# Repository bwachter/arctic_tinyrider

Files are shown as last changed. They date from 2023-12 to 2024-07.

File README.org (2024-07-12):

* Arctic Tinyrider                                                    :TOC_4:
  - [[#introduction][Introduction]]
  - [[#transmitter-setup][Transmitter setup]]
  - [[#wiring][Wiring]]

** Introduction
This is a program to provide more fine grained control for the [[https://www.printables.com/model/114300-arctic-tinyrider-rc-snowmobile][Arctic Tinyrider RC snowmobile]]. It uses an Arduino to talk to the receiver module via the iBus protocol - which requires a compatible receiver (typically FlySky).

My setup uses:

- one Arduino nano
- one FS-A8S receiver

For full functionality this assumes using a receiver with 8 channels, though some features can be disabled, making it work on receivers with 6 and even 4 channels.

Features are:

- throttle and steering (obviously)
- ignition switch: throttle is pinned to zero unless ignition switch is on. This allows somewhat safer handling when not fully switched off. A LED connected to D13 will signal throttle state by blinking (off) or solid light (on).
- control remapping: a three state switch can be used to change controls
- dynamic speed control: a dial can be used to limit the speed without having to change the throttle curve in the transmitter. In the default setting the transmitter starts with 50% output, and can be set up to 100%.

The last three features can be disabled at compile time, freeing up channels.

Default control setup uses the left stick up/down for throttle, right stick sideways for steering. The second switch position of the control switch flips sticks - note that the right stick centers in all directions, so when switching to that a speed controller without reverse will be running at half throttle already. The third switch position will put both throttle and steering on the right switch.

Planned work includes:
- support some more LEDs
- support failsafe modes in transmitters which have that

** Transmitter setup

To use all features your transmitter should have the channels configured like this:

1. right stick, left/right
2. right stick, up/down
3. left stick, up/down (range changes based on throttle curve)
4. left stick, left/right
5. left dial VRA
6. right dial VRB
7. SWA
8. SWC

VRA/VRB are configured on channels 5/6 per default in 'aux channel setup', while the switches are not assigned. VRB is currently not used - to make this work with a 6 channel receiver remove the VRB mapping, decide which of the 3 additional features you want to drop, adjust mappings for channel 5/6, and adjust the source code.

Note that both throttle curve and trim settings will mess with the values sent by the transmitter - and probably should all be disabled.

** Wiring

You'll need one power and one ground bar to connect everything to. A cheap variant would be two pin headers with a wire soldered over the pins.

The three-pin connector from the ESC connects to power bar, ground bar, and pin D3 on the Arduino.

The servo connects to power bar, ground bar, and pin D10 on the Arduino.

Depending on your receiver you may have dedicated VCC/ground connectors, if not just connect power and ground from any channel to power/ground bars. Connect the iBus pin to the RX pin on the Arduino. Note that when flashing via USB this pin must be disconnected while flashing.

On the Arduino connect ground and VIN to ground/power bars.

The following table contains the basic setup. If you don't want to add any LEDs you can skip the link part, otherwise it is sensible to provide a ground pin to connect to a separate ground bar for additional LEDs. When using LEDs drawing more than 20µA or more than two for one effect they'll have to be switched via transistor and powered via the ESC, in which case it also makes sense to lead out a power bar:

|          | GND | 5v | arduino |
|----------+-----+----+---------|
| ESC      | x   | x  | D3      |
| receiver | x   | x  | RX      |
| arduino  | x   | x  |         |
| servo    | x   | x  | D10     |
| link     | x   | x  |         |

When adding LEDs the default pins are in this table. D13 is also the LED mounted on the Arduino, so if this one is visible no external LEDs are needed. If it is not visible at least one status-LED should be connected for safety - this LED signals throttle lock or error conditions. In a full LED setup the status LEDs should be used as rear lights.

|        | Pin 1 | Pin 2 |
|--------+-------+-------|
| status | D13   | D2    |
| front  | D11   | D12   |
| effect | D4    | D5    |

Pins are set up to minimise gaps, soldering three three-pin-headers will cover all pins on one side, while connecting the unused RST pin. On the other side just VIN and D13 need to be populated.

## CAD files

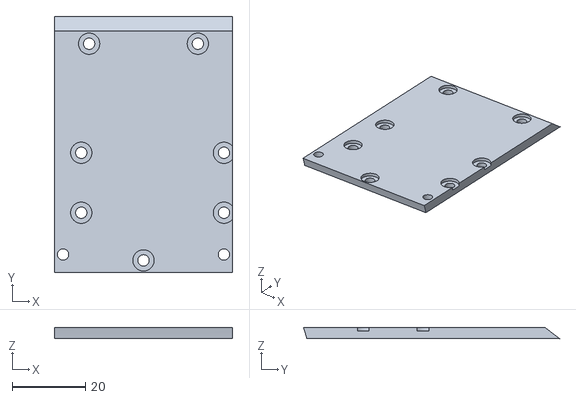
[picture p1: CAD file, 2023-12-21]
top plate.stl
48.6 x 69.7 x 3.00

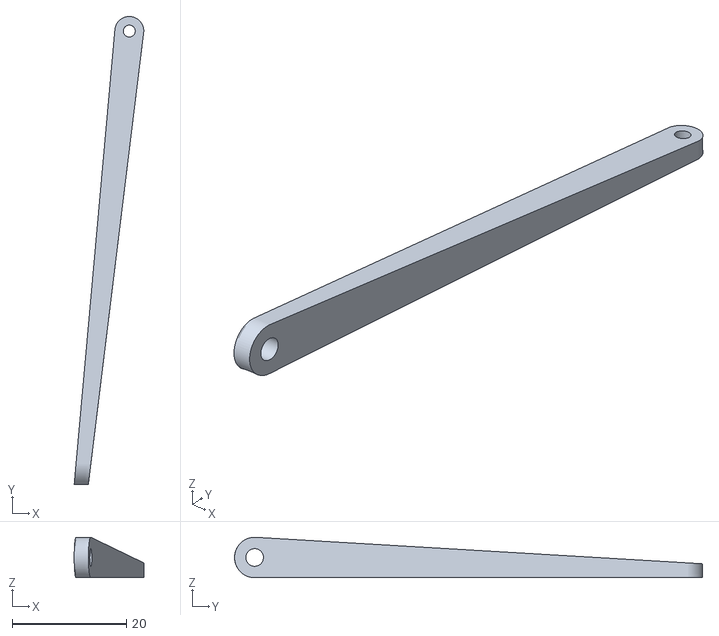
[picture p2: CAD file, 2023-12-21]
rod linkage hard x2.stl
12.2 x 82.1 x 7.10

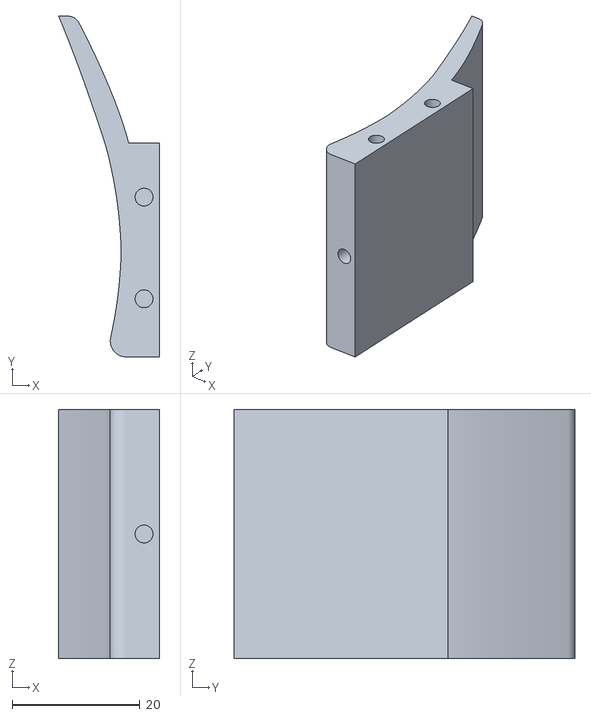
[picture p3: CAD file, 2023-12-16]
seat.stl
15.8 x 53.4 x 39.0

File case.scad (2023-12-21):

use <lego/LEGO.scad>;

layers=1;

x=58.5;
y=69;
h=3;
screw=3;

brick_height=9.6;
top=(brick_height*layers)+3;

$fn=25;

module support_triangle(side_length, side_height){
  polygon(points=[[0,0],[side_height,side_length],[side_height,0]], paths=[[0,1,2]]);
}

translate([-33.5,-4])
import("top plate.stl");

difference(){
  union(){
    // right side bottom plate
    translate([-23.5,0,0]){
      cube([23.5,51,3]);
    }

    // left side bottom plate
    translate([48.5, 14,0]){
      cube([23.5,37,3]);
    }
    translate([48.5, 0,0]){
      cube([3,30,3]);
    }
    // outside wall left side
    color("green") translate([48.5, -5,0]){
      cube([3,21,12.0]);
    }
    translate([-23.5,-5,0]){
      cube([75,5,3]);
    }
    translate([-23.5,10,0]){
      cube([75,3,3]);
      translate([75,-11,3])
        rotate([90,0,270]) {
        color("green")
          linear_extrude(75){
          support_triangle(5, 5);
        }
      }
    }

    // small triangle supporting the sloped brick on the left
    translate([-3.5,19,0]){
      translate([75.5,-9,3])
        rotate([90,180,270]) {
        color("green")
          linear_extrude(22){
          support_triangle(3, 4.5);
        }
      }
    }

    translate([24.2,55,3]){
      // front 6
      color("white") place(0, 0, 0) block(
        block_bottom_type="closed",
        width=1,
        length=6
        );
      // right 4
      color("white") uncenter(0,1) place(-1, -4, 0) block(
        block_bottom_type="closed",
        width=1,
        length=5
        );
      // left 4
      color("white") uncenter(0,1) place(-1, 3, 0) block(
        block_bottom_type="closed",
        width=1,
        length=5
        );
      // right technics brick
      color("white") uncenter(0, 1) rotate([0,0,90])
        place(6, -4, 0) block(
          horizontal_holes=true,
          block_bottom_type="closed",
          width=1,
          length=5
          );
      // this is a double brick to avoid a gap for more stability
      color("green") uncenter(1, 1) rotate([0,0,90])
        place(6, -8, 0) block(
          block_bottom_type="closed",
          width=1,
          length=2
          );
      // left  brick
      color("white") uncenter(0, 1) rotate([0,0,90])
        place(-5, -3, 0) block(
          horizontal_holes=true,
          block_bottom_type="closed",
          width=1,
          length=3
          );
      // back brick
      color("white") uncenter(0, 1)
        place(-8, -2, 0) block(
          block_bottom_type="closed",
          width=1,
          length=9
          );
      // brick over the gears
      color("red")
        uncenter(1,1)
        rotate([0,0,90])
        place(-4, -7, 0) block(
          block_bottom_type="closed",
          width=3,
          length=4
          );
      if (layers >= 2){
        // second layer
        color("white") uncenter(1, 1) place(-1, 2, 1) rotate([0,0,90]) block(
          block_bottom_type="closed",
          width=1,
          length=2
          );
        color("white") uncenter(1, 1) place(-1, -3, 1) rotate([0,0,90]) block(
          block_bottom_type="closed",
          width=1,
          length=2
          );
        color("white") place(0, 0, 1) block(
          block_bottom_type="closed",
          width=1,
          length=4,
          horizontal_holes=true
          );
        // right side
        color("white") place(-1, -4, 1) block(
          horizontal_holes=true,
          block_bottom_type="closed",
          width=1,
          length=2
          );
        color("white") uncenter(0, 1) rotate([0,0,90])
          place(6, -1, 1) block(
            block_bottom_type="closed",
            width=1,
            length=1
            );
        color("white") uncenter(1, 1) rotate([0,0,90])
          place(6, -3, 1) block(
            horizontal_holes=true,
            block_bottom_type="closed",
            width=1,
            length=2
            );
        color("white") uncenter(1, 1) rotate([0,0,90])
          place(6, -5, 1) block(
            block_bottom_type="closed",
            width=1,
            length=2
            );

        color("white") uncenter(1, 1) rotate([0,0,90])
          place(6, -7, 1) block(
            horizontal_holes=true,
            block_bottom_type="closed",
            width=1,
            length=2
            );
        // left side
        color("white") place(-1, 4, 1) block(
          horizontal_holes=true,
          block_bottom_type="closed",
          width=1,
          length=2
          );
        color("white") uncenter(0, 1) rotate([0,0,90])
          place(-5, -1, 1) block(
            block_bottom_type="closed",
            width=1,
            length=1
            );
        color("white") uncenter(1, 1) rotate([0,0,90])
          place(-5, -3, 1) block(
            horizontal_holes=true,
            block_bottom_type="closed",
            width=1,
            length=2
            );
        color("white") uncenter(1, 1) rotate([0,0,90])
          place(-5, -5, 1) block(
            block_bottom_type="closed",
            width=1,
            length=2
            );
        color("white") uncenter(1, 1) rotate([0,0,90])
          place(-5, -7, 1) block(
            horizontal_holes=true,
            block_bottom_type="closed",
            width=1,
            length=2
            );
        // back
        color("white") uncenter(0, 1)
          place(-8, -6, 1) block(
            block_bottom_type="closed",
            width=1,
            length=1
            );
        color("white") uncenter(0, 0)
          place(-8, -4, 1) block(
            horizontal_holes=true,
            block_bottom_type="closed",
            width=1,
            length=2
            );
        color("white") uncenter(0, 0)
          place(-8, -2, 1) block(
            block_bottom_type="closed",
            width=1,
            length=2
            );
        // center block
        color("white") uncenter(0, 0)
          place(-8, 0, 1) block(
            horizontal_holes=true,
            block_bottom_type="closed",
            width=1,
            length=2
            );
        color("white") uncenter(0, 0)
          place(-8, 2, 1) block(
            block_bottom_type="closed",
            width=1,
            length=2
            );
        color("white") uncenter(0, 0)
          place(-8, 4, 1) block(
            horizontal_holes=true,
            block_bottom_type="closed",
            width=1,
            length=2
            );
        color("white") uncenter(0, 1)
          place(-8, 5, 1) block(
            block_bottom_type="closed",
            width=1,
            length=1
            );
      }
    }
  }

  // differences come here
  translate([-23.5,10,0]){
    translate([100,-15,3])
      rotate([90,0,270]) {
      linear_extrude(115){
        support_triangle(10, 10);
      }
    }
  }

  translate([50,-15,-40])
    rotate([0,90,0])
    cylinder(r=50, h=30);

  // cutout for screw head
  translate([46,4,3])
    cylinder(r=3, h=30);

  // the cutouts always are on the top most layer
  // cutout for ESC power cable
  translate([64,25.4,top-8.2])
    cube([10,3,9]);

  // cutout for the servo
  translate([38.4,41,top-4.2])
    cube([2,18,7]);

}

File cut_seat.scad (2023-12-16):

difference(){
  translate([-300, -134.99, 0])
    import("seat.stl");

  cube([30,30,50]);
}

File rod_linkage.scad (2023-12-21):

$fn=30;

difference(){
  translate([-200,-100,0])
    import("rod linkage hard x2.stl");

  translate([10.1,84.1,0])
  cylinder(r=3, h=1.6);
}

  translate([10.1,84.1,2.2]){
    difference(){
      cylinder(r=2.5, h=1.5);
      cylinder(r=1.1, h=2);
  }
}

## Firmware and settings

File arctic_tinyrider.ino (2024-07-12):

#include <IBusBM.h>
#include <Servo.h>

/*
 The further you go down the defines the less likely you should
 want to change something.

 Channel numbers are C indexes, i.e., one less than your transmitter
 shows you.

 PWM values are based on the servo library, ranging from 0 to 180 - not
 the native 0-255 of Arduino PWM (which is a wrong frequency).
*/

//#define ESC_PWM_REVERSED 1

// the digital pin the motor is attached to
#define MOTOR_PIN 3

// the digital pin the servo is attached to
#define SERVO_PIN 10

// arduino can tolerate about 20µA per pin, with a total of 200µA
// a bright 5mm LED draws roughly 20µA - so three sets of two LEDs
// should be safe. If you need more connect them to power directly,
// and trigger them via transistor

// the power LEDs also serve as back lights
#define POWER_LED 13
#define POWER_LEDS {2,13}
#define FRONT_LEDS {11,12}
#define EFFECT_LEDS {4,5}

// this should be a three state switch, and needs to be setup as aux channel
// comment this definition if you don't want that feature
#define CONTROL_CHANNEL 7

// a two state switch, preventing throttle to engage unless switched on
// comment this definition if you don't want that feature
#define IGNITION_CHANNEL 6

#define EFFECT_CHANNEL 5

/*
  This configures an input (default: VRA on channel 5) to adjust the speed
  curve.

  The speed curve itself needs adjustment below and recompilation to change.
  Default settings have roughly half the maximum speed with VRA on zero, going
  up to full speed with VRA on max.

  Comment the SPEED_CHANNEL definition if you don't want that.
*/
#define SPEED_CHANNEL 4
#define SPEED_MIN 90
#define SPEED_MAX 180

// time LED should remain in a specific status. This is per loop - so
// take LOOP_DELAY into account as well.
#define LED_DELAY 10
// slightly delays the loop to allow time for mechanical elements to
// move, at cost of slight input delay.
#define LOOP_DELAY 20

#define PWM_MIN 0
#define PWM_MAX 180

// with trim the values sent by the transmitter might be over/under this range,
// but this is good enough for now
#define RX_MIN 1000
#define RX_MAX 2000

IBusBM IBus;
Servo steeringServo;
Servo motor;
int ignition=1000;
int led_state=0;
int throttle_channel;
int steering_channel;
int failsafe_channel;
int reverse_channel;

int power_leds[]=POWER_LEDS;
int front_leds[]=FRONT_LEDS;
int effect_leds[]=EFFECT_LEDS;

enum led_effects{
  led_on,
  led_off,
  led_cycle
};

void setup_controls(){
#ifdef CONTROL_CHANNEL
  int controls = IBus.readChannel(CONTROL_CHANNEL);
#else
  int controls = 1000;
#endif
  if (controls == 1500){
    // throttle right, steering left
    throttle_channel=1;
    steering_channel=3;
    failsafe_channel=0;
    reverse_channel=2;
  } else if (controls == 2000) {
    // throttle and steering right
    throttle_channel=1;
    steering_channel=0;
    failsafe_channel=3;
    reverse_channel=2;
  } else {
    // default, throttle on the left, steering right
    throttle_channel=2;
    steering_channel=0;
    failsafe_channel=3;
    reverse_channel=1;
  }
}

void set_led(int leds[], int cycle, int effect){
  switch(effect){
    case led_on:
      digitalWrite(leds[0], HIGH);
      digitalWrite(leds[1], HIGH);
      break;
    case led_off:
      digitalWrite(leds[0], LOW);
      digitalWrite(leds[1], LOW);
      break;
    case led_cycle:
      if (cycle < 0){
        digitalWrite(leds[0], LOW);
        digitalWrite(leds[1], LOW);
      } else {
        digitalWrite(leds[0], HIGH);
        digitalWrite(leds[1], HIGH);
      }
      break;
  }
}

void setup() {
  pinMode(POWER_LED, OUTPUT);
  IBus.begin(Serial);
  steeringServo.attach(SERVO_PIN);
  motor.attach(MOTOR_PIN, 1000, 2000);
  motor.write(0);
  setup_controls();
}

void loop() {
  if (led_state >= LED_DELAY)
    led_state = LED_DELAY*-1;
  led_state++;

  setup_controls();

  int steer;
  steer = IBus.readChannel(steering_channel);
  Serial.print("Steer: ");
  Serial.print(steer);
  if (steer >= 1000 and steer <= 2000)
    steeringServo.writeMicroseconds(steer);
  else
    steeringServo.writeMicroseconds(1500);

#ifdef IGNITION_CHANNEL
  ignition = IBus.readChannel(IGNITION_CHANNEL);
  if (ignition != 2000){
    motor.write(0);

    set_led(power_leds, led_state, led_cycle);
  } else {
#endif
    set_led(power_leds, led_state, led_on);
    int throttle;
    throttle = IBus.readChannel(throttle_channel);
    Serial.print(" Throttle: ");
    Serial.print(throttle);
    int pwm = map(throttle, RX_MIN, RX_MAX, PWM_MIN, PWM_MAX);
    Serial.print(" ");
    Serial.print(pwm);
#ifdef SPEED_CHANNEL
    int pwm_max_raw = IBus.readChannel(SPEED_CHANNEL);
    int pwm_max = map(pwm_max_raw, RX_MIN, RX_MAX, SPEED_MIN, SPEED_MAX);
    int pwm_adjusted = map(throttle, RX_MIN, RX_MAX, PWM_MIN, pwm_max);
    Serial.print(" adjusted ");
    Serial.print(pwm_adjusted);
    motor.write(pwm_adjusted);
#else
    motor.write(pwm);
#endif
#ifdef IGNITION_CHANNEL
  }
#endif

  int failsafe = IBus.readChannel(failsafe_channel);
  Serial.print(" failsafe ");
  Serial.print(failsafe);
  Serial.println();

  delay(LOOP_DELAY);
}

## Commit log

2023-12-16 Add shortened seat module
    This includes the original seat.stl from https://www.printables.com/model/114300-arctic-tinyrider-rc-snowmobile
    [cut_seat.scad, seat.stl]
2023-12-21 Add modified rod linkage
    [rod linkage hard x2.stl, rod_linkage.scad]
2023-12-21 Add case module
    [case.scad, top plate.stl]
2023-12-21 Add multiple LED pins per function
2024-07-12 Disable steering on bad input
2024-07-12 Add basic effect LED support
2024-07-12 Switch servo pin
